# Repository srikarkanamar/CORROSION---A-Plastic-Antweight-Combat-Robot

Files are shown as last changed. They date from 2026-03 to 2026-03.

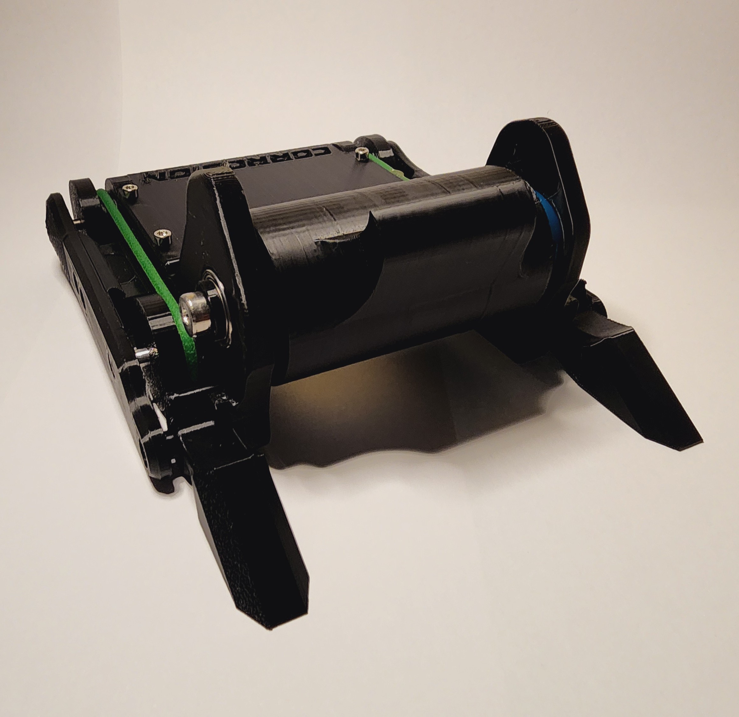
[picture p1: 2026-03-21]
PHOTOS/20260315_214731.jpg

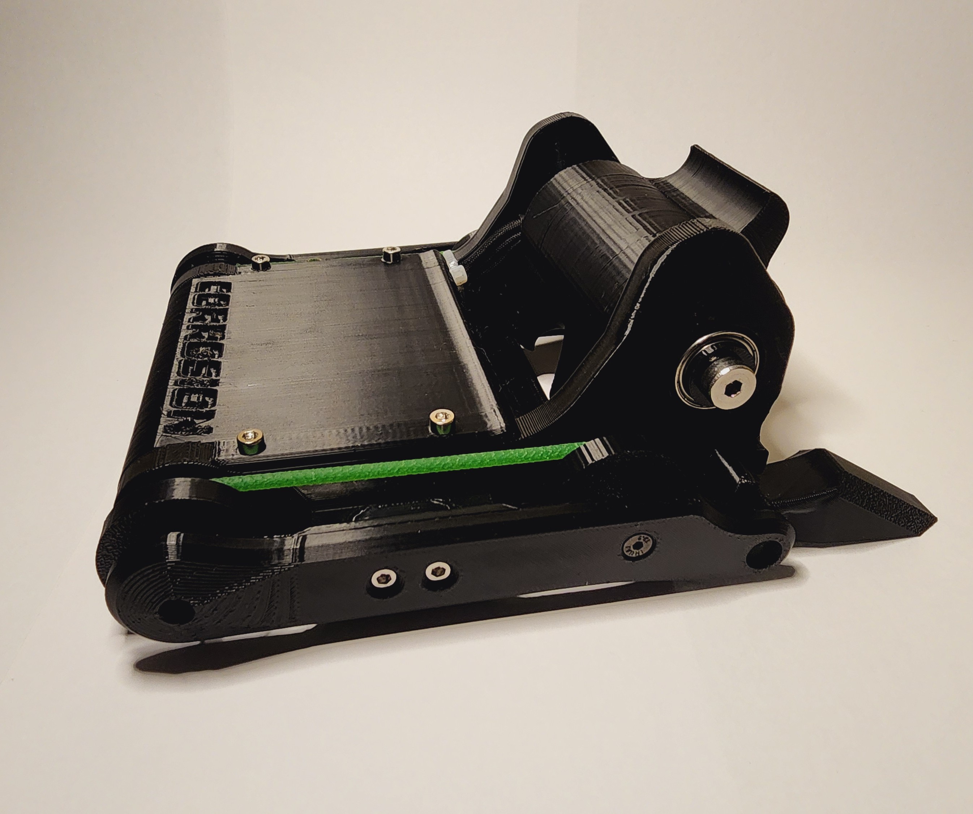
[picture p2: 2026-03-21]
PHOTOS/20260315_214711.jpg

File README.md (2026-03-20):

# CORROSION---A-Plastic-Antweight-Combat-Robot

CORROSION PLASTIC ANTWEIGHT COMBAT ROBOT DOCUMENTATION

Project Overview:

CORROSION is a 1lb plastic antweight combat robot designed and built completely from scratch to participate in the competitive combat robotics scene. The robot is a four-wheel drum spinner, a popular archetype, augmented by defensive design and weapon optimization. This document covers the entire research, design, and build process of CORROSION, as well as the groundwork for further development.

Preliminary Research and Organization:

Through joining communities and online servers, I networked and learned from veteran competitors and individuals who had gone to the global stage competing in BattleBots™, at the largest open-division scale of combat robotics (250lb). From these valuable mentors, I managed to learn troves of information that can only be learned through experience, as well as insight into modern, novel strategies fellow builders are exploring. Engaging in these forums and servers enabled me to have designs critiqued by experts in their craft and receive advice on subsequent development.

To decide on the framework of my robot, I analyzed the current competition scene with available quantitative metrics. The first source I examined was the main organizer of the United States events’ rankings for the most successful bots. These rankings were not based on subjective analysis, but rather on a scoring based on win rate scaled with the rankings of opposing bots. Interestingly, the titleholders of each year were mostly, if not all, drum spinners. This is largely thanks to the division’s rules and their implications on robot design. Because bots are prohibited from using contact weapons that are not entirely composed of 3D-printed plastics, convergent designs of large spinning masses for engagement emerged. These designs aim to circumvent plastic’s low density and strength by creating larger contact areas and higher inertia.

Defensive and more technical designs, like shell-spinners, lifters, and grabbers, are disadvantaged by the unforgiving weight restrictions, the physical properties of legal FDM plastics, and the inability to pose a strong offensive front. Drum spinners are prominent because they are highly successful, due to their robust designs, powerful offensive strategy, and simple driving. 

In another dimension of design strategy, I decided to use a 4WD belted wheel system for my bot’s drivetrain. I settled on this model after evaluating weight, cost, ease of repair, and maneuverability.

Weight + General Considerations:

Although 2WD models occupy much less weight, they often bear smaller drums and weapons, as a result of their collapsed drivetrain. Because I aimed to create a large drum spinner, I settled on 4WD. However, traditional 4WD requires 4 motors for control, subtracting additional weight for extra motors, larger batteries, and more complex electronics, from the already scarce limit of 1lb (~ 454 grams). To leverage the power of this setup, while also minimizing weight, I implemented a belted system. This entirely removes the conventional requirements and creates a resilient, fault-tolerant drivetrain. Although the two belted front wheels create a strong grip for the bot to execute strikes and evasive maneuvers, even if the belted system fails, the fault-tolerant design retains 2WD capabilities with the directly driven motors. 

Cost:

Additional brushed drive motors are one of the highest costs for my bot’s design. An expensive, fully direct-driven bot would hinder me from participating in many tournaments and would stress my tight budget. The belted system runs on polyurethane belts and small, lathed axles, both of which are highly economical.

Ease of Repair:

A higher quantity of electronics and motors creates more points of failure for the bot to encounter in the arena. Furthermore, in the pits, where competitors are only given 20 minutes to complete their repairs, additional motors and complex electronics would be more time-consuming to troubleshoot and fix. Belted drive reduces the number of actively powered elements, allowing me to prioritize repair time on more pressing matters.

Maneuverability:

I chose a 4WD over a 2WD because of the inherent gyroscopic effects created by drum-spinners. Because the weapon drums are the largest component of a bot and spin at hundreds of RPM, they generate a gyroscopic effect that makes bots tilt violently as they turn. 4WD systems are objectively better at negating gyro-effects, leveraging their wide and stable driveframes. Meanwhile, 2WD spinners are often downsized to reduce gyroscopic interference,  which is non-negotiable for my “big stick” design strategy.

Design and Part Breakdown:

Uprights:

Well-designed uprights (most commonly used term for the two parallel vertical structures that frame the entire bot) are instrumental to success. This was not only the first part I designed, but also the one most iterated upon. I designed my uprights to house all of my motors and an external shell to create an easily replaceable structure that is “hot-swappable.” Because uprights are the most structurally significant component, I decided to prioritize strength over weight savings by adding extra material in the form of higher walls and infill. After several iterations, I landed on 3 walls and 15% sparse gyroid infill.

Side Armor:

The side armor of the bot is designed to mitigate impact as much as possible. To design effectively under the weight restriction, I implemented novel design techniques to reduce deformation and failure on impact. The first design choice I made was to run both metal axles through the armor, as well as two M3s to the uprights, in order to create a stable base. I adjusted the design to be optimized for horizontal spinner bots by reducing any type of harsh angles that spinners can catch onto. By printing in an unconventional orientation, I designed armor that chips, rather than bends under high-force impacts. Deformation of the armor could destabilize my drivetrain, leading to a plethora of disadvantages across the bot. After consulting with fellow competitors, I augmented my design to contain soft curves that create geometries that vertical spinners cannot “bite”. These surfaces result in glancing hits that fail to transfer lethal energy, giving my bot the upper hand in defensive interaction. 

Wedgelets:

CORROSION’s weapon thrives when given a point to snag and transfer as much energy as possible. This common principle, shared across vertical spinner designs has led to the development of forks and wedges. These slanted components aim to slip under opposing robots, lifting them slightly at an angle, creating a perfect point on the underside of an opponent for the weapon to impart as much energy as possible. Conventionally, in non-plastic open division events, bots use small metal wedges known as “forks” to lift up opponents. However, this design doesn’t effectively translate to CORROSION’s division, as plastics are brittle and easily break under impact. In order to create an effective “ground game,” I designed wedgelets, which merge the advantages of spanning wedges and sharp forks. The wedgelets’ dense structure allows them to sustain impact and effectively dissipate forces across the frame. Their size reduces weight, but is large enough to effectively get under competitor bots. The slanted edges allow for a greater range of direction on approaches, improving the success rate of this component.  The hook-like structure at the top acts as a limiter to prevent the bot from high-centering itself on the wedgelets.

Bottom/Top Plate:

The bottom and top plates are very simple geometries composed largely of solid infill. Because both of them cover a large surface area and all of the internal electronics, I took time to design them effectively within the weight limit. The top plate is almost entirely solid, protecting the bot from overhead spinners and impacts when immobilized. The bottom plate was designed to have grates in order to help with quick inspection, but against powerful vertical spinners, it can be interchanged with a solid version. The top plate also forms the “scoop” under the high-speed weapon. Because the front of my bot has a large spinning mass, the back of CORROSION is its most vulnerable area. However, the bot’s agility should allow it to protect this region well enough to last a round.

Weapon and Design:

The weapon is the most technically designed element of the entire bot. The following is basic knowledge necessary to understand weapon geometry:

The weapon must have its center of mass centered on its rotational axis. If it is unbalanced, it will vibrate violently, break, or impart power spikes in the motor. 
The weapon’s tooth size (the length of its hooking element) dictates the amount of “bite” it gets, and the force imparted on opponents.
Concentrating mass far from the center of a spinning body generates maximum moment of inertia (therefore, power) per gram.
The bot’s weapon is the only element that is completely solid, which means optimization to save weight is paramount.
Asymmetric weapon geometries receive better bite than symmetrical geometries

The design process of CORROSION’s weapon underwent many iterations, starting with an asymmetrical design, transferring to a symmetrical design, and later becoming a hybrid of both. This weapon design is novel and is currently being pioneered among a few other builders I contacted and worked with. Here is a breakdown of all iterations:

Asymmetrical:

CORROSION’s first weapon design was an asymmetrical drum that prioritized bite. It was composed of a center unit, a long tooth, and an equally heavy counterweight. Because CORROSION’s drum profile is very wide, the single geometry extruded weapon would definitely incur severe drag and apply motor strain, even when spinning completely unobstructed. Since every gram of material at the edge costs multiple grams of counterweight material, which is closer to the spinning axis, the weapon became unreasonably heavy. Any reductions in weight would mean reducing the strength of the tooth, which was a tradeoff I wasn’t willing to accept. During this design process, I experimented with possibly adding a smaller tooth to the counterweight, an idea that sparked future development in multi-tooth strategies.

Symmetrical:

The symmetrical design was very similar to the asymmetrical design, with a single extruded profile. Two smaller teeth created a more aerodynamic spinning body, but bite and, therefore, power transfer were attenuated. The entire strategy for CORROSION’s design was creating a lethal offensive force to compensate for vulnerabilities in defense, so this idea was scrapped. During the design process, I experimented with hollowing a small portion of the center to save weight, whilst still retaining structural integrity, a concept I would later apply to my final design.

Hybrid:

My engineering strategy for this project revolved around fusing together the strengths of different approaches to create a bot that could endure complex challenges. For my final weapon design, I merged elements from the asymmetrical and symmetrical designs. I created a drum with a multiprofile setup. The teeth were essentially slightly bolstered and lengthened versions of the symmetrical design, but instead of having one extruded geometry, I created portions on each side of the central cylindrical mass. This solved the issue of bite, as each region of impact on the weapon had only one potential tooth to deliver hits. Furthermore, this reduced a significant amount of weight compared to the symmetrical design. I furthered this by porting the hollow segment approach from the symmetrical design to the final, hybrid weapon. By creating large fillets across the teeth, I created  a smooth, drag-resistant geometry that can also handle large stress concentrations on impacts. Because the shear strength of filament printed in a continuous segment is higher than the shear strength between multiple layers (held only by layer adhesion), an optimal print orientation on the profile face was chosen. 

The weapon is directly driven by a Repeat Robotics™ 2822 brushless motor, a reliable and widely used component in the antweight class. The traditional weapon axle design was scrapped for a more modular ball bearing ring design. The weapon directly interfaces with this ball bearing ring for free movement, and is internally structurally supported by an M5 shoulder bolt. I, notably, had much frustration tweaking tolerances for clearance and proper interfacing, requiring multiple prints to get right. 

Wheels/Drive:

I am using two Repeat Robotics™ Mini Brushed Mk2s to handle belted drives for the bot. In order to achieve a polished belted drive, I used two dead axles (Repeat Robotics™ Drive Axle Ants) for the passive wheels. All of the wheels have a “canal” that allows me to link them using polyurethane belting. Although at first glance the friction-based system may look subpar to tooth-driven counterparts, this system prevents motor burnout by limiting torque at the belt’s threshold. I am currently researching and developing the best tire for these wheels, with the current promising prospects being rubber sheets and O-rings. I am limited from casting tires with silicon, because all non-plastic parts must be off the shelf, according to local rulebooks.

Groundwork for Future Development and Areas to Improve:

Electronics:
Although all electronics for this build are plug-and-play, I have yet to configure them in their entirety and connect them with the bot’s active components. I will be using an ELRS radio system, which is currently gaining popularity in the builder community over legacy CC2500 systems. The newer ELRS (controlled by my Radiomaster Pocket Controller) is more accessible and easier to troubleshoot, has better range and latency specs, and is highly supported through its open-source software. I aim to experiment with the additional functionalities and presets that are available. Furthermore, I will be using open-source AM32 ESCs over older closed-source BLHELI_32s to leverage better control on the lower ends of power. 

Situational Configurations:
Although Corrosion is generally designed to handle a large variety of bot types, creating specialized configurations can improve performance. For example, against an overhead spinner, side armor is completely ineffectual, but by removing side armor, weight can be saved to repurpose by thickening and strengthening critical areas like the top plate. 

Clearance/Warping Issues:
Because of the limitations of FDM home systems, like the Bambu Lab A1 that I am currently using, thin parts and cylindrical cavities printed perpendicularly to the build plate are often subject to warping. This is attributed to the contraction of plastics as they cool, and although unavoidable, they are mitigatable. Currently, I face minimal issues, other than the rare hole that is too large to tap screws, but in hindsight, I wish I had optimized the interface points for 3D printing. At this current stage, it is unrealistic and futile to edit my entire system, but I will carry this insight into later projects and designs. 

Slicer Modifiers:
Slicers such as Bambu Studio offer simple modifiers, configurable regions where the slicer follows an alternate ruleset. This would come in handy to prioritize material and strength in higher-risk areas and reduce weight in areas that rarely come into contact with opponents. Currently, I am using part-generalized slicing, like the large majority of competitors, but this is an avenue I would like to explore. However, highly optimized builds like these are better suited for open weight classes, where modifiers can be used to alter the flex points of material like TPU. In the current PLA+ version of the bot, these changes would be largely insignificant and inconsistent for the extensive time it would take to implement.

Current Status as of March 19, 2026:

Hardware for the bot is completely finalized and polished. The bot is seven grams underweight from previous estimates, which is good news and allows for buffer weight when installing electronics. The weapon assembly is balanced, and access to new tools (electric screwdriver, precision drills, higher-quality fasteners) has sped up the development process.

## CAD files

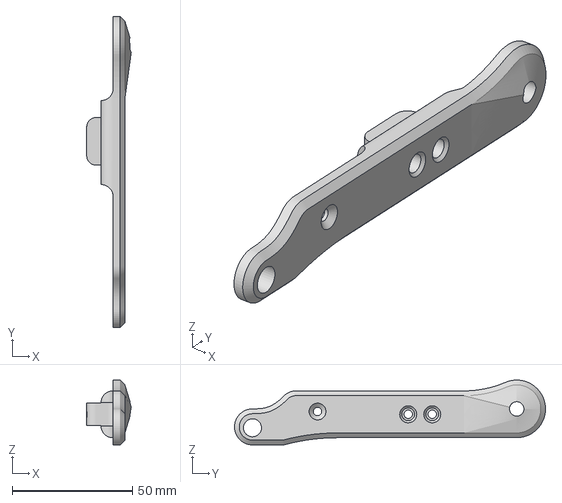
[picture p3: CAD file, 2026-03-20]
CAD_FILES/SIDE_ARMOR/LEFT_SIDE_ARMOR.3mf
18.6 x 129.5 x 27.0 mm

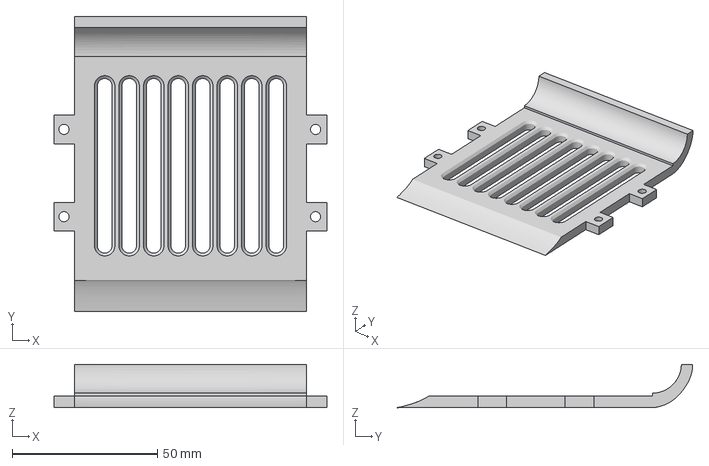
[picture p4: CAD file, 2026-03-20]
CAD_FILES/TOP+BOTTOM_PLATES/BOTTOM_PLATE.3mf
93.8 x 101.6 x 14.9 mm

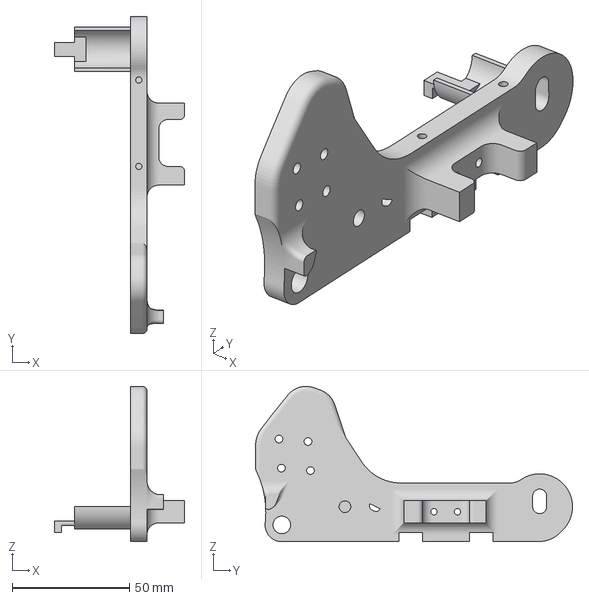
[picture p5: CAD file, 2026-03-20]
CAD_FILES/UPRIGHTS/LEFT_UPRIGHT.3mf
55.5 x 135.1 x 66.2 mm

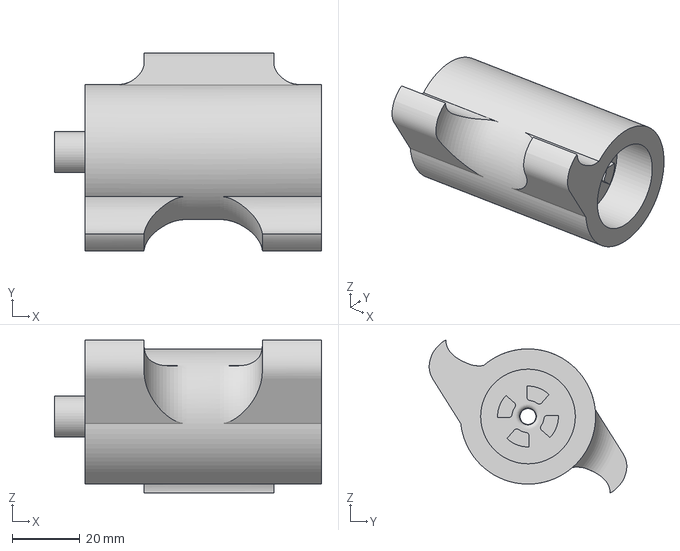
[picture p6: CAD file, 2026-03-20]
CAD_FILES/WEAPON/WEAPON.3mf
79.0 x 58.5 x 45.2 mm

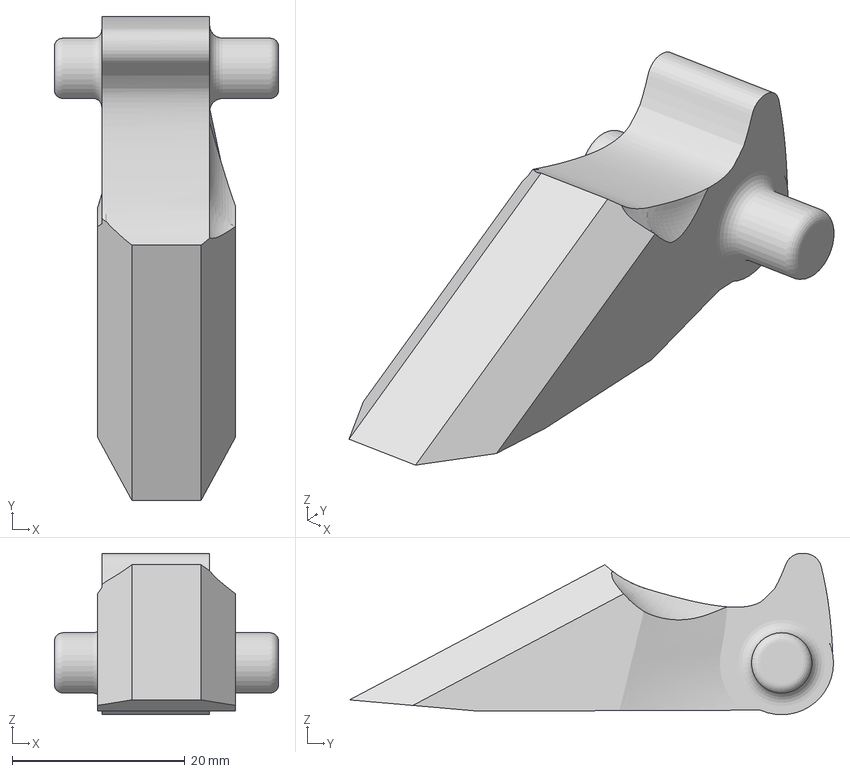
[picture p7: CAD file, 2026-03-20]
CAD_FILES/WEDGELETS/LEFT_WEDGELET.3mf
26.0 x 56.1 x 18.7 mm

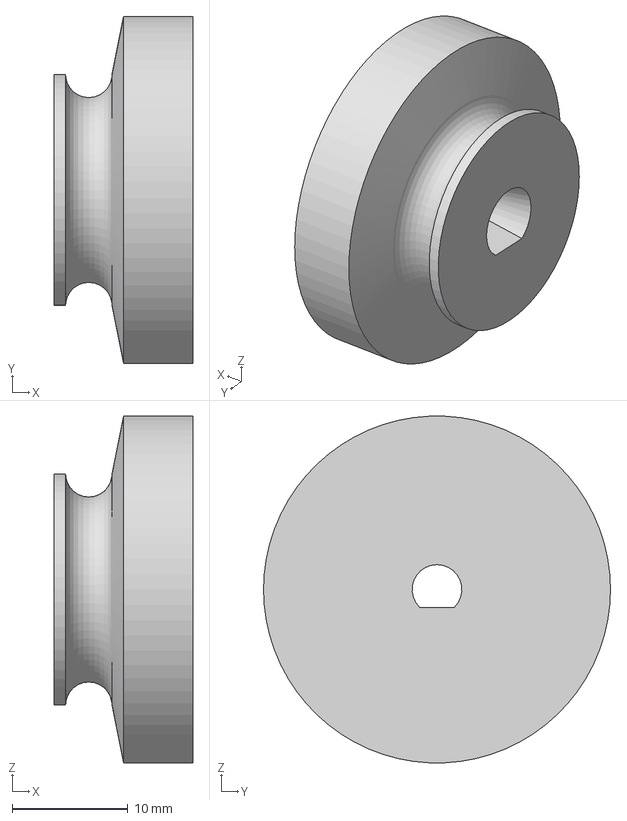
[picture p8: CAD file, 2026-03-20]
CAD_FILES/WHEELS/BACK_WHEEL.3mf
12.0 x 30.0 x 30.0 mm

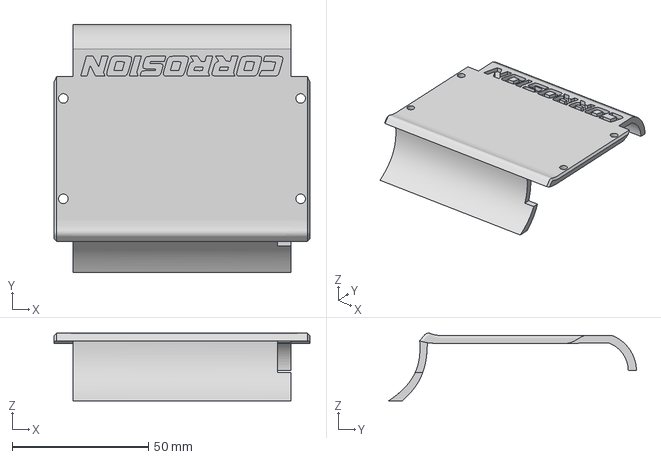
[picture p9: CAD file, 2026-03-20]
CAD_FILES/TOP+BOTTOM_PLATES/TOP_PLATE.3mf
93.8 x 90.9 x 24.8 mm

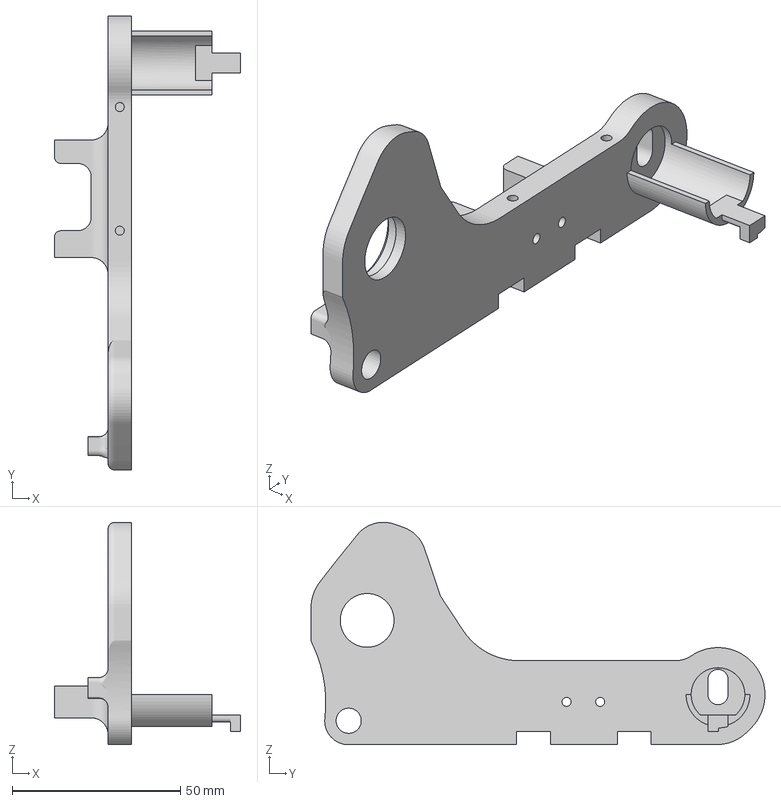
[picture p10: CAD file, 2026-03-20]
CAD_FILES/UPRIGHTS/RIGHT_UPRIGHT.3mf
55.5 x 135.1 x 66.2 mm

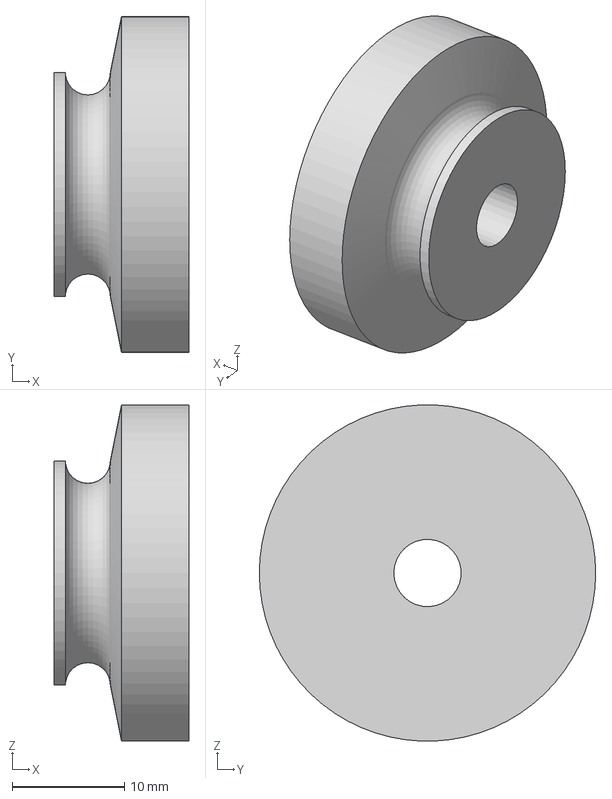
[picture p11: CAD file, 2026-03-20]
CAD_FILES/WHEELS/FRONT_WHEEL.3mf
12.0 x 30.0 x 30.0 mm

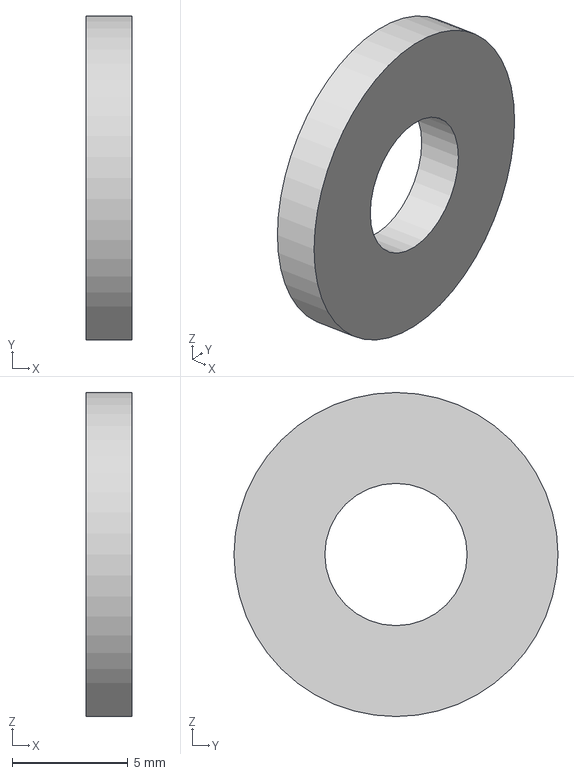
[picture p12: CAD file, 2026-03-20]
CAD_FILES/WEAPON/WEAPON_RETENTION_WASHER.3mf
2.00 x 14.0 x 14.0 mm

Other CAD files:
CAD_FILES/SIDE_ARMOR/RIGHT_SIDE_ARMOR.3mf
CAD_FILES/WEDGELETS/RIGHT_WEDGELET.3mf
